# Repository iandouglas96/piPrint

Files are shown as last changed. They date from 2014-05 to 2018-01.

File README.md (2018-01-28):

# NOTE:
piPrint development ceased a while ago.  I no longer have the hardware that this code was built to run.  Consider the code unsupported and undeveloped, though feel free to still email me with questions.

# piPrint (v0.3a)
## Run your 3D Printer with only a Raspberry Pi

Ian D. Miller
info [at] pxlweavr [dot] com
http://www.pxlweavr.com

Kenan Bitikofer
kbitikofer [at] gmail [dot] com

## Warning
piPrint is currently under heavy development.  It seems to be working fairly well at the moment, but is not considered stable.  If you just want to get a 3D Printer up and running, consider looking at other options at http://www.reprap.org.

## Documentation
A video of piPrint in action is here: http://youtu.be/JW6yJvLF7Jk  It gives a general ideas of the capabilites and interface of the printer.

Put the files contained in the server directory on the pi.  Edit server.py to change the ip address at the bottom to whatever the pi's address is.  If using a different thermistor from the Honeywell 100K, update the temp lookup table in TempSensor.py.  Pin assignments can also be set at the top of server.py.  When this configuration is complete, run

    sudo python server.py
    
It isn't a bad idea to add this to your .profile to run on startup.

In piPrintControl.py, change the top two ip addresses to the address of your pi, then, on another computer, run

    python piPrintControl.py
    
You will then be able to remotely control the printer over the local network.

NEW: piPrint now supports laser engraving.  To engrave, hook up a laser driver circuit to the hotend pins.  Files with the .ngc extension are assumed to be laser engraving files from Inkscape GCodeTools, and will be treated accordingly.

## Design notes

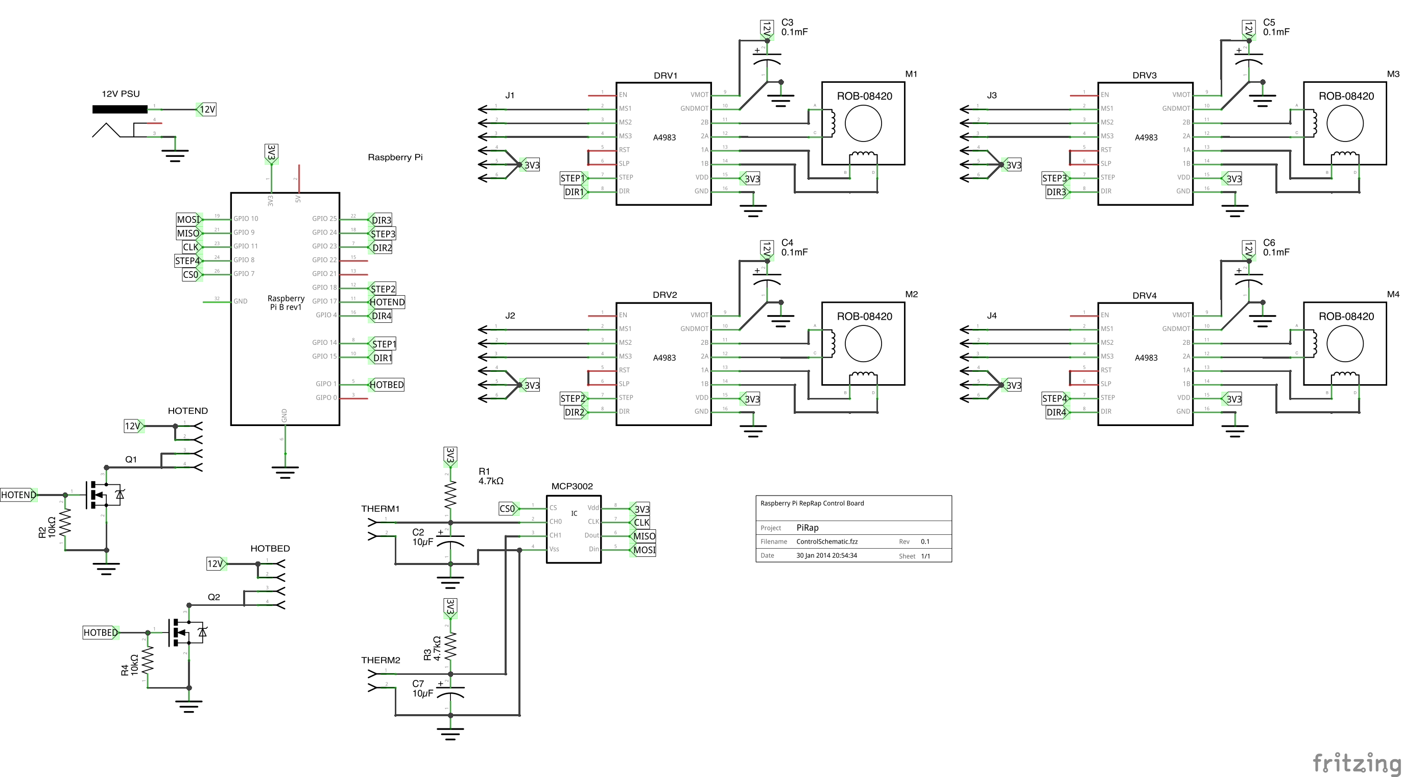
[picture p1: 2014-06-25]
Design/controlSchem.png

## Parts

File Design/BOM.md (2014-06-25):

##Useful Links

* http://reprap.org/wiki/WolfStrap - WolfStrap instructions
* http://reprap.org/mediawiki/images/f/f5/Sanguinololu_1.3a.png - Wiring schematic (hotend and thermistor control parts most relevant)
* http://www.pololu.com/product/1182 - Stepper control information, incl. datasheet
* http://slic3r.org - Seems like the standard software used to generate GCode instructions from a 3D model file
* http://www.marginallyclever.com/blog/2013/08/how-to-build-an-2-axis-arduino-cnc-gcode-interpreter/ - Information on writing a GCode interpreter.

##Bill of Materials (based on WolfStrap)

###Electronics

* Raspberry Pi (Model A or B) (1)
  - $25.00 or $35.00 from favorite vendor
* piPrint control PCB (1)
  - https://oshpark.com/shared_projects/540EpEYK
  - $60.00 for 3 from OSHPark
* Stepper Drivers (4)
  - http://www.ultibots.com/pololu-a4988-stepper-motor-driver/
  - $10.00 each
* MCP3002 ADC Converter
  - https://www.sparkfun.com/products/8636
  - $2.30
* Other misc. discrete components (See wiring schem.)
  - $15.00

####Subtotal
**$152.30**

###Specialty Hardware

* Drive Pulleys (2)
  - Connect the motor to the belt.  Have teeth for accuracy
  - http://www.ultibots.com/gt2-timing-pulley-20-tooth-economy-aluminum/
  - $5.00 each
* Idler Pulleys (2)
  - Connect other side of belt.  Not driven, so do not have teeth, but do have bearings to reduce friction.
  - http://www.ultibots.com/v-slot-smooth-idler-pulley-kit/
  - $5.00 each
* Timing Belts (2)
  - http://www.ultibots.com/gt2-timing-belt-1164mm/
  - $10.00 each
* Shaft Coupler (1)
  - http://www.ultibots.com/motor-shaft-coupling/ 
  - $8.95
* Threaded Rod (1)  Kenan can maybe get from C Clamp
  - http://www.ultibots.com/z-axis-leadscrew-nut-pair/
  - $35.00 
* Stepper Motors (3)
  - http://www.ultibots.com/kysan-nema-17-stepper-motor/
  - $16.95 each
* Extruder kit (1)
  - https://nwreprap.com/product/15/
  - $100.00

####Subtotal
**$234.80**

###General Hardware (for WolfStrap)
*These are estimates and may be on the high side of things

* Cabinet rails (3 sets)
  - Local hardware store
  - $15.00 for a set
* Screws and bolts (various)
  - $20.00
* Wood (various, very much up to the builder)
  - $50.00

####Subtotal
**$115.00**

###Total
**~$500.00**

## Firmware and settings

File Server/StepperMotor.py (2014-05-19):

import wiringpi2

class Stepper:
    stepPin=0 #pin numbers
    dirPin=0
    def __init__(self,stepPin,dirPin):
    	#initial a Bipolar_Stepper_Moter objects by assigning the pins
        wiringpi2.wiringPiSetupPhys()
        
        self.stepPin=stepPin
        self.dirPin=dirPin
        
        wiringpi2.pinMode(self.stepPin,1)
        wiringpi2.pinMode(self.dirPin,1)
        print "Stepper Configured"   
        
    def move(self, direction1, delay):
		if direction1==1:
			wiringpi2.digitalWrite(self.dirPin, 1);
		else:
			wiringpi2.digitalWrite(self.dirPin, 0);    
		wiringpi2.digitalWrite(self.stepPin,0)
		wiringpi2.delayMicroseconds(int(delay//2))
		wiringpi2.digitalWrite(self.stepPin,1)
		wiringpi2.delayMicroseconds(int(delay//2))

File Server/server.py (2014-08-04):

import spidev
import wiringpi2
from StepperMotor import Stepper
import time
#import serial
import thread
#from math import *
from numpy import pi, sin, cos, sqrt, arccos, arcsin
import TempSensor
import xmlrpclib
from SimpleXMLRPCServer import SimpleXMLRPCServer

x = Stepper(18,22)
y = Stepper(12,16)
z = Stepper(24,7)
e = Stepper(8,10)

wiringpi2.wiringPiSetupPhys()

spi = spidev.SpiDev()
spi.open(0,1)

heatpin=11
fanpin=5
wiringpi2.pinMode(heatpin, 1)
wiringpi2.pinMode(fanpin, 1)
wiringpi2.digitalWrite(fanpin, 0) #Fan off
TEMP=-1

#These values convert from steps to mm
xcalib=8*1000/200.0  #steps/mm
ycalib=8*1000/200.0  #steps/mm
zcalib=10000/100.0 #steps/mm
ecalib=4*10000/195.0  #steps/mm(pulled extrusion)

#Acceleration
jerkG = 25.0 #mm/sec start speed, cannot be 0
accel = 1000.0 #mm/sec/sec

#Engraving TODO: read from GCODE
eSpeed = 50 #mm/min

#Internal settings
zadjust=0
temp=0
lineNum=0
totalLines=0
isHeating=False
isPrinting=False
engraving=False

nextdx = 0
nextdy = 0
nextdz = 0
nextde = 0
nextf = 1200.0
dx = 0
dy = 0
dz = 0
de = 0
f = 1200.0
dt0 = 1000
x_pos = 0
y_pos = 0

#port = serial.Serial("/dev/ttyAMA0", baudrate=38400, timeout=3.0) #Open serial connection to ADC

# def GCD(a,b):#greatest common divisor
# 	while b:
# 	   a, b = b, a%b;
# 	return a;
# 
# def LCM(a,b):#least common multipler
# 	if a == 0:
# 		return b;
# 	if b == 0:
# 		return a;
# 	return a*b/GCD(a,b);

def sign(a): #return the sign of number a
	if a>0:
		return 1;
	elif a<0:
		return -1;
	else:
		return 0;
		
def dot(x1,y1,x2,y2):
	mag = sqrt(x1**2 + y1**2)*sqrt(x2**2 + y2**2)
	if mag == 0:
		return 0
	dot = float(x1*x2+y1*y2)
	if dot < 0:
		return 0
	return dot/mag

def Vertical_Motor_Step(stepper3, dz, speed):
	"""Much simpler this one is.  Just move it."""
	#global pos
	dir3=-sign(dz)
	dz=abs(dz)
	for i in range(0, int(dz)):
		stepper3.move(dir3,1000000.0/speed);
	#print pos
	return 0;

def Horizontal_Motor_Step(stepper1, dx, stepper2, dy, stepper3, de, f):
	global dt0
#   TODO extrusion rate
#   control stepper motor 1 and 2 simultaneously
#   stepper1 and stepper2 are objects of StepperMotor class
#   direction is reflected in the polarity of [dt] or [dy]
	dir1=sign(dx);  #get dirction from the polarity of argument [step]
	dir2=sign(dy);
	dir3=-sign(de); #direction backwards for stepper

	dx=int(abs(dx));
	dy=int(abs(dy));
	de=int(abs(de));

# [total_micro_step] total number of micro steps
# stepper motor 1 will move one step every [micro_dt] steps
# stepper motor 2 will move one step every [micro_dy] steps
# So [total_mirco_step]=[micro_dt]*[dt] if dt<>0;  [total_micro_step]=[micro_dy]*[dy] if dy<>0 
	if dx==0 and dy==0 and de==0:
		return 0;
	else:
		totalSteps=dx+dy+de
		micro_dx=totalSteps+5
		micro_dy=totalSteps+5
		micro_de=totalSteps+5

		if dx!=0: micro_dx=totalSteps/float(dx);
		if dy!=0: micro_dy=totalSteps/float(dy);
		if de!=0: micro_de=totalSteps/float(de);
	
	D = sqrt((dx/xcalib)**2+(dy/ycalib)**2)
	T = D/f #Time in sec
	if T == 0 and de != 0:
		T = (abs(de)/ecalib)/(f)	

	dtMax = (T*1000000.0)/totalSteps #Convert to us
	jerk = 1+jerkG + dot(nextdx,nextdy,dir1*dx,dir2*dy)*(f-jerkG) #Add one, since not / by 0
	
	if (dx != 0 or dy != 0) and f>jerk:
		dtf = (D*1000000.0)/(totalSteps*jerk)
		accelDist = (f**2 - jerk**2)/(2*accel)
		accelSteps = accelDist*(totalSteps/D)
		dtdt = (dtf-dtMax)/accelSteps
	else:
		dt0 = dtMax
		dtdt = 0
		accelSteps = 0
	
	dt = dt0
	step = 0
	#xmoved, ymoved, emoved= 0, 0, 0
	# print 'Total iteration steps =',total_micro_step
	for i in range(0, totalSteps):
		if (dx!=0 and i % micro_dx<1):#motor 1 need to turn one step
			stepper1.move(dir1,dt);
			step += 1
			#xmoved+=1
			
		if (dy!=0 and i % micro_dy<1):#motor 2 need to turn one step
			stepper2.move(dir2,dt);
			step += 1
			#ymoved+=1

		if (de!=0 and i % micro_de<1):
			stepper3.move(dir3,dt);
			step += 1
			#emoved+=1
		
		if (totalSteps-step < accelSteps):
			if (dt < dtf+dtdt):
				dt += dtdt
			else:
				dt = dtf
		elif (dt > dtMax+dtdt):
			dt -= dtdt
		else:
			dt = dtMax
				
	dt0 = dt
	
	# print xmoved, ymoved, emoved
# 	print dt, dy, de
	return 0;
	
def get_adc(channel):
	# Only 2 channels 0 and 1 else return -1
	if ((channel > 1) or (channel < 0)):
		return -1
	# Send start bit, sgl/diff, odd/sign, MSBF
	# channel = 0 sends 0000 0001 1000 0000 0000 0000
	# channel = 1 sends 0000 0001 1100 0000 0000 0000
	# sgl/diff = 1; odd/sign = channel; MSBF = 0
	r = spi.xfer2([1,(2+channel)<<6,0])
   
	# spi.xfer2 returns same number of 8 bit bytes
	# as sent. In this case, 3 - 8 bit bytes are returned
	# We must then parse out the correct 10 bit byte from
	# the 24 bits returned. The following line discards
	# all bits but the 10 data bits from the center of
	# the last 2 bytes: XXXX XXXX - XXXX DDDD - DDDD DDXX
	ret = ((r[1]&31) << 6) + (r[2] >> 2)
	return ret
	
	
def controlTemp():
	global temp
	global isHeating
	#Prints ADC Val to terminal
	while True:
		if not engraving:
			adc = get_adc(0)
			temp= TempSensor.getTemp(adc)
			if temp > 0 and temp < 240: #Are we getting reasonable numbers?
				if temp>TEMP:
					isHeating = False
					wiringpi2.digitalWrite(heatpin, 0)
				else:
					isHeating = True
					wiringpi2.digitalWrite(heatpin, 1)
			else:
				wiringpi2.digitalWrite(heatpin, 0)
				# print "Didn't receive response.  Killing heat."

		time.sleep(1)

def wait_for_temp():
	global isPrinting
	while temp < TEMP-1:
		print str(temp)+","+str(TEMP)
		if not isPrinting:
			break
		time.sleep(2)

def get_info():
	return [temp, lineNum, totalLines, isHeating]
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

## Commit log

2014-05-19 v0.2a
    Improved speed control, now using wiringpi2-python for more accurate
    timing. Added projected time remaining to client software. Gerber
    files for piPrint board added.
    [ControlSchematic.fzz]
2014-05-20 v0.2.1a
    Added acceleration support. Much higher print speeds are now
    attainable with less shudder.
2014-06-04 v0.2.3a
    Bug fixes for client software
    [server.py]
2014-06-13 Update README.md
    Added link to video of printer.
2014-06-25 Improved Hardware Docs
    [ControlSchematic.fzz]
2014-06-25 Update BOM.md
    Fixed formatting
2014-08-04 v0.3a
    Added support for laser cutting and engraving. Some other minor bug
    fixes and improvements.
    [server.py]
